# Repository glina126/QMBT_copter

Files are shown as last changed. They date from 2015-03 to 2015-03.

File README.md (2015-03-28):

# QMBT_copter
A simple, yet versatile quadcopter controller and code. Based on the Arduino platform using the Atmega328p and MPU6050.

arduino quadcopter
arduino quadcopter

QMBT with its code in the background

##Final Update:
This project is changing direction. The atmega328p microcontroller is simply insufficient for being used as a quadcopter brain. <br>
This is due to a few reasons mainly because - not enough interrupts and 8bit architecture.  <br>
The loop runs at a mere 33 miliseconds, which is not sufficient.  <br>
Also, due to the lack of interrupts, the precision at which we can sample the RC RX is very low causing noise in the system. <br>
That being said, the project is changing gears and moving on to a much better microcontroller, LPC11U35 Cortex-m0 running at 48mhz. <br> 

###This project has a few milestones that are set on its path. 
1. Create a versatile PCB which will overcome the common problems such as power distribution. 
2. Create lightweight code that will be self sufficient, aka, no external program will be needed for changing settings of the quadcopter, except for a terminal window. 
3. Ultimate goal is to have full support of peripheral devices such as a sonic distance sensor to help aid in obstacle avoidance, or a GPS unit for man-less operation. 

This is just the beginning of the project, though experimentation with the PCB have been conducted for a while now. At this point, the project is reset to a fresh start.

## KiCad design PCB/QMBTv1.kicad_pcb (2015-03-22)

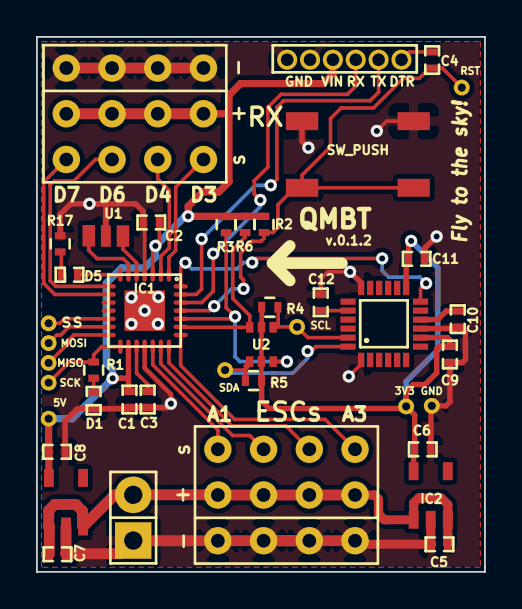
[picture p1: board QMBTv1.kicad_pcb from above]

Board: 2 copper layers, 24.9 x 29.7 mm, 42 parts (0 on the bottom side), 33 nets.

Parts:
C1, C2, C3, C4, C10, C11: 0.1uF; SMD-0402_c
C5: 1uF; SMD-0402_c
C6: 2.2uF; SMD-0402_c
C7, C8: C; SMD-0402_c
C9: 10nF; SMD-0402_c
C12: 2.2nF; SMD-0402_c
C13: 6pin_1.27mm
D1, D5: LED; SMD-0402_LED
IC1: ATMEGA328P-MM; QFN-28-4x4mm_fixed_mask
IC2, IC3: MCP1802_(Vreg); Sot-23-5
IC4: MPU6050
P9: MISO; 1x0.5mm_Through_hole2
P10: MOSI; 1x0.5mm_Through_hole2
P11: SCK; 1x0.5mm_Through_hole2
P12: RST; 1x0.5mm_Through_hole2
P14: SDA; 1x0.5mm_Through_hole2
P15: SCL; 1x0.5mm_Through_hole2
P16: SS; 1x0.5mm_Through_hole2
P17: VCC; Socket_Strip_Straight_1x02
P18: 3V3; 1x0.5mm_Through_hole2
P19: GND; 1x0.5mm_Through_hole2
P20: 5V; 1x0.5mm_Through_hole2
R1, R3, R4, R5, R6, R17: 1K; R_0402
R2: 10K; R_0402
SW1: SW_PUSH; switch_tactile_SM10
U1: ceramic_resonator; ceramic_resonator_smd
U2: BSS138DW_array
U3, U4: conn_3x4

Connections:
+3.3V: C6.1, C9.1, C11.1, IC2.5, IC4.8, IC4.13, P18.1, R4.1, R5.1, U2.2, U2.5
+5V: C1.1, C2.1, C8.1, C13.3, IC1.3, IC1.16, IC3.5, P20.1, R2.1, R3.1, R6.1, U3.5
A0: IC1.19, U4.1
A1: IC1.20, U4.2
A2: IC1.21, U4.3
A3: IC1.22, U4.4
D2: IC1.28, IC4.12
D3: IC1.1, U3.1
D4: IC1.2, U3.2
D5: D5.1, IC1.7
D6: IC1.8, U3.3
D7: IC1.9, U3.4
D10: IC1.12, P16.1
DTR: C4.1, C13.6
GND: C1.2, C2.2, C3.2, C5.2, C6.2, C7.2, C8.2, C9.2, C10.2, C11.2, C12.2, C13.1, C13.2, D1.2, IC1.4, IC1.18, IC1.d29, IC2.2, IC3.2, IC4.1, IC4.9, IC4.18, P17.1, P19.1, R17.1, SW1.2, U1.3, U3.6, U4.6
H_SCL: IC1.24, R3.2, U2.6
H_SDA: IC1.23, R6.2, U2.3
MISO: IC1.14, P9.1
MOSI: IC1.13, P10.1
unnamed: C3.1, IC1.17
unnamed: C10.1, IC4.10
unnamed: C12.1, IC4.20
unnamed: D1.1, R1.1
unnamed: D5.2, R17.2
unnamed: IC1.5, U1.1
unnamed: IC1.6, U1.2
RESET: C4.2, IC1.25, P12.1, R2.2, SW1.1
RXI: C13.4, IC1.26
SCK: IC1.15, P11.1, R1.2
SCL: IC4.23, P15.1, R4.2, U2.1
SDA: IC4.24, P14.1, R5.2, U2.4
TXD: C13.5, IC1.27
VIN: C5.1, C7.1, IC2.1, IC2.3, IC3.1, IC3.3, P17.2, U4.5

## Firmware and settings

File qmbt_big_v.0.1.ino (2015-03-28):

/****************************************************************************************
QMBT BIG V.1.0 - stable
Written by Damian Glinojecki

Features:
- Arming system 
- Flexible code to easily accommodate different structure and internals
- Spin wild (best feature!)
- Flyable, but hard to control quadcopter 
- IT WORKS! 

TO DO:
- Change platform - MBED
- Next platform is going to be a 32-bit ARM Cortex-M0 Microcontroller running at 48MHz 
- Prototyipng platform: http://developer.mbed.org/platforms/EA-LPC11U35/
- Finally getting out of the Arduino bubble. 
****************************************************************************************/

#include <Servo.h>
#include "I2Cdev.h"  // library written by jrowberg
#include "MPU6050.h" // library written by jrowberg
#include <PID_v1.h>  // library written by Beauregard

#if I2CDEV_IMPLEMENTATION == I2CDEV_ARDUINO_WIRE
    #include "Wire.h"
#endif

#define AILERON 3  // RX in pin
#define ELEVATOR 4 // RX in pin
#define RUDDER 7   // RX in pin
#define THROTTLE 6 // RX in pin

#define M1 14 // ESC motor pin 
#define M2 15 // ESC motor pin 
#define M3 16 // ESC motor pin 
#define M4 17 // ESC motor pin 

#define MIN_OUTPUT 1000 // min output in microseconds
#define MAX_OUTPUT 2000 // max output in microseconds

#define MIN_LIMIT -100 // the minimum value outputed by the PID
#define MAX_LIMIT 100  // the maximum value outputed by the PID

#define MIN_SPIN 1200 // minimal motor speed

#define INVERT_CHANNEL 3000 // constant used for inverting the channel output

MPU6050 mpu;
Servo motor[4];

// global vars
int16_t ax, ay, az; // raw values of the accelerometer output
int16_t gx, gy, gz; // raw values of the gyroscope output

uint32_t timer; // used to keep track of time
unsigned long start_time = 0; // used to measure loop cycle time in ms

double raw_x_degree = 0; // raw x angle in degrees
double raw_y_degree = 0; // raw y angle in degrees
double raw_z_degree = 0; // raw z angle in degrees

double comp_x_degree = 0; // complimentary x angle in degrees
double comp_y_degree = 0; // complimentary y angle in degrees
double comp_z_degree = 0; // complimentary z angle in degrees

double acc_x_degree = 0; // angle estimated using the accelerometer 
double acc_y_degree = 0; // angle estimated using the accelerometer

int rx_duration_last[4] = {1500,1500,1500,1000}; // used to average channels and for comparesment - safety mechanism
int rx_duration[4]; // store the ms each channel output

double input_gx, output_gx, setpoint_gx; // x axis PID
double input_gy, output_gy, setpoint_gy; // y axis PID
double input_gz, output_gz, setpoint_gz; // z axis PID

int motor_speed[4] = {MIN_OUTPUT, MIN_OUTPUT, MIN_OUTPUT, MIN_OUTPUT}; // timing of a pulse - in microseconds 
int throttle = 0; // throttle position

// PID objects
PID gx_pid(&input_gx,&output_gx,&setpoint_gx,1.8,2.0,.4,DIRECT); // 1.2, 1.0, .65
PID gy_pid(&input_gy,&output_gy,&setpoint_gy,1.8,2.0,.4,DIRECT); // 1.4, 0.9, 0.44
PID gz_pid(&input_gz,&output_gz,&setpoint_gz,1.2,0,.41,DIRECT);

// tunning variables
double pid_tune_p = 0.0;
double pid_tune_i = 0.0;
double pid_tune_d = 0.0;

bool ARMED = false; // protection against accidental motor spin
int arm_led = 5; // arm led - on when ARMED

void setup() {
  // initialize input pins
  pinMode(AILERON, INPUT);
  pinMode(ELEVATOR, INPUT);
  pinMode(RUDDER, INPUT);
  pinMode(THROTTLE, INPUT);
  
  // arm led - on when ARMED
  pinMode(arm_led, OUTPUT);
   
  // attach motor to pins
  motor[0].attach(M1);
  motor[1].attach(M2);
  motor[2].attach(M3);
  motor[3].attach(M4);
  
  // turn off all motors
  motor[0].writeMicroseconds(MIN_OUTPUT);
  motor[1].writeMicroseconds(MIN_OUTPUT);
  motor[2].writeMicroseconds(MIN_OUTPUT);
  motor[3].writeMicroseconds(MIN_OUTPUT);
  
  // join I2C bus (I2Cdev library doesn't do this automatically)
  #if I2CDEV_IMPLEMENTATION == I2CDEV_ARDUINO_WIRE
      Wire.begin();
  #elif I2CDEV_IMPLEMENTATION == I2CDEV_BUILTIN_FASTWIRE
      Fastwire::setup(400, true);
  #endif
 
  // initialize serial comm
  Serial.begin(38400);
  
  // initialize mpu6050
  mpu.initialize();
  
  // verify connection
  Serial.println("Testing device connections...");
  Serial.println(mpu.testConnection() ? "MPU6050 connection successful" : "MPU6050 connection failed");
  
  // set gyroscope and accelerometer ranges - safe to do it everytime?
  #if 1
    mpu.setFullScaleGyroRange(0x00);
    mpu.setFullScaleAccelRange(0x00); 
    mpu.setDLPFMode(0x03); //0x03
    
    Serial.print("gyro rate: ");
    Serial.println(mpu.getFullScaleGyroRange());
    Serial.print("accel rate: ");
    Serial.println(mpu.getFullScaleAccelRange());
    Serial.print("DLPFMode: ");
    Serial.println(mpu.getDLPFMode());
    delay(1500);
  #endif
  
  // initialize PID
  input_gx = output_gx = setpoint_gx = 0; // x axis PID
  input_gy =  output_gy = setpoint_gy = 0; // y axis PID
  input_gz = output_gz = setpoint_gz = 0; // z axis PID
  // set up PID for x axis
  gx_pid.SetOutputLimits(MIN_LIMIT,MAX_LIMIT); //MIN and MAX for output limits 
  gx_pid.SetSampleTime(30);
  // set up PID for y axis
  gy_pid.SetOutputLimits(MIN_LIMIT,MAX_LIMIT); 
  gy_pid.SetSampleTime(30);
  // set up PID for yaw axis
  gz_pid.SetOutputLimits(MIN_LIMIT,MAX_LIMIT);
  gz_pid.SetSampleTime(30);
  
  // initialize the timer 
  timer = micros(); 
}

void loop() {  
  // start timing loop
  start_time = millis();
    
  // get the user input
  getUserInput();
  
  arm();
  
  // populate new filtered values
  callIMU();
  
  // calculate the PID values
  callPID();
  
  // calculate new motor values 
  calculateNewMotorValues();
  
  // apply the new values to the motors
  applyToMotors();
       
  // display time per loop cycle 
  #if 0
    Serial.print("loop cycle time = ");
    Serial.println(millis() - start_time);
  #endif
  
}

void callIMU()
{
  // read raw acceletometer and gyro measurements from mpu6050
  mpu.getMotion6(&ax, &ay, &az, &gx, &gy, &gz);
  
  // check how much time has gone by
  double dt = (double)(micros() - timer) / 1000000; 
  
  // update the timer
  timer = micros(); 
  
  // display raw mpu values
  #if 0
    Serial.print("a/g:\t");
    Serial.print(ax); Serial.print("\t");
    Serial.print(ay); Serial.print("\t");
    Serial.print(az); Serial.print("\t");
    Serial.print(gx); Serial.print("\t");
    Serial.print(gy); Serial.print("\t");
    Serial.println(gz);
  #endif
  
  // calculate the angles 
  
  // convert to degrees per second
  double gyro_x_rate = gx / 131.0; 
  double gyro_y_rate = gy / 131.0; 
  double gyro_z_rate = gz / 131.0;
  
  // display degrees per second of the xyz axies
  #if 0
    Serial.print("gx/gy/gz in deg/sec = ");
    Serial.print(gyro_x_rate); Serial.print("\t");
    Serial.print(gyro_y_rate); Serial.print("\t");
    Serial.println(gyro_z_rate);
  #endif
  
  // raw gyro values in degrees
  raw_x_degree += gyro_x_rate * dt; // Calculate gyro angle without any filter
  raw_y_degree += gyro_y_rate * dt;
  raw_z_degree += gyro_z_rate * dt;
  
  // display raw degrees of the xyz axies (non-filtered)
  #if 0
    Serial.print("gx/gy/gz in deg = ");
    Serial.print(raw_x_degree); Serial.print("\t");
    Serial.print(raw_y_degree); Serial.print("\t");
    Serial.println(raw_z_degree);
  #endif
  
  // convert to angles using the accelerometer  
  acc_x_degree = atan((double) ay / sqrt((double) ax * (double) ax + (double) az * (double) az)) * RAD_TO_DEG;
  acc_y_degree = atan2((double) -ax, (double) az) * RAD_TO_DEG;
  
  // display angles estimated using the accelerameter
  #if 0
    Serial.print("ax/ay in deg = ");
    Serial.print(acc_x_degree); Serial.print("\t");
    Serial.println(acc_y_degree);
  #endif
  
  // apply complimentary filtering - kalman is too hefty for this this mcu when using pulseIn :( 
  comp_x_degree = 0.93 * (comp_x_degree + gyro_x_rate * dt) + 0.07 * acc_x_degree; // Calculate the angle using a Complimentary filter
  comp_y_degree = 0.93 * (comp_y_degree + gyro_y_rate * dt) + 0.07 * acc_y_degree;
  comp_z_degree = raw_z_degree; // no magnometer thus we cannot filter the z axis. :(
  
  // display angles estimated using the complimentary filter
  #if 1
    Serial.print("compl angles x/y/z  = ");
    Serial.print(comp_x_degree); Serial.print("\t");
    Serial.print(comp_y_degree); Serial.print("\t");
    Serial.println(comp_z_degree);
  #endif
    
}

void getUserInput()
{
  // check whats going on all the rx channels  
  // read in the 4 supported channels 
  rx_duration[0] = pulseIn(AILERON, HIGH);
  rx_duration[1] = pulseIn(ELEVATOR, HIGH);
  rx_duration[2] = pulseIn(RUDDER, HIGH);
  rx_duration[3] = INVERT_CHANNEL - pulseIn(THROTTLE, HIGH);
  
  // save teh rx duration before modifying
  int rx_temp[4];
  rx_temp[0] = rx_duration[0];
  rx_temp[1] = rx_duration[1];
  rx_temp[2] = rx_duration[2];
  rx_temp[3] = rx_duration[3];
  
  // smoothing and safety algorithm - average of the last 2 - average of the last 3 would probably better (or even a filter)
  for(int i = 0; i < 4; i++)
  {
    if(rx_duration[i] - rx_duration_last[i] > 1000)
    {
      // this is not normal. disable the quadcopter
      // not implemented for now. 
    }
    else
    {
      // average the two values together
      rx_duration[i] = (rx_duration[i] + rx_duration_last[i])/2;     
      
      // save the current value to the old one
      rx_duration_last[i] = rx_temp[i];
    }
  }
   
  // diplay miliseconds for each channel
  #if 0
    Serial.print("A/E/R/T = ");
    Serial.print(rx_duration[0]);
    Serial.print("\t");
    Serial.print(rx_duration[1]);
    Serial.print("\t");
    Serial.print(rx_duration[2]);
    Serial.print("\t");
    Serial.println(rx_duration[3]);
  #endif
}

void callPID()
{ 
  // set the new setpoint 
  long temp_n = -40.0;
  long temp_p = 40.0;
  setpoint_gx = modifiedMap(rx_duration[1], MIN_OUTPUT, MAX_OUTPUT, temp_n, temp_p);
  setpoint_gy = modifiedMap(rx_duration[0], MIN_OUTPUT, MAX_OUTPUT, -40, 40);
  setpoint_gz = modifiedMap(rx_duration[2], MIN_OUTPUT, MAX_OUTPUT, -40, 40);
      
  // display setpoint before the calculation
  #if 0
    Serial.print("PID setpoint x/y/z = "); 
    Serial.print(setpoint_gx);
    Serial.print("\t"); 
    Serial.print(setpoint_gy);
    Serial.print("\t"); 
    Serial.println(setpoint_gz);
  #endif
  
  
  // set new input
 input_gx = comp_x_degree;
 input_gy = comp_y_degree;
 input_gz = comp_z_degree;
  
  // display input_gx before the calculation
  #if 0
    Serial.print("PID input x/y/z = "); 
    Serial.print(input_gx);
    Serial.print("\t"); 
    Serial.print(input_gy);
    Serial.print("\t"); 
    Serial.println(input_gz);
  #endif
  
  // compute the PID
  gx_pid.Compute();
  gy_pid.Compute();
  gz_pid.Compute();
    
  // display raw PID values
  #if 0
    Serial.print("PID x/y/z = "); 
    Serial.print(output_gx);
    Serial.print("\t"); 
    Serial.print(output_gy);
    Serial.print("\t"); 
    Serial.println(output_gz);
  #endif
  
}

void calculateNewMotorValues()
{
  // motor_speed is to be applied to the motors.
  // we have to make sure it has been properly filtered
  // programmers fingers are really important :P
  
  // set the throttle straight from the rx
  throttle = rx_duration[3]; // number between 1000 and 2000 (theoritically) 
  
  // all motors get throttle and then are corrected by the PID
  motor_speed[0] = throttle + output_gx + output_gy ;
  motor_speed[1] = throttle + output_gx - output_gy ;
  motor_speed[2] = throttle - output_gx - output_gy ;
  motor_speed[3] = throttle - output_gx + output_gy ;
  
  // make sure that the values are in range
  for(int i = 0; i < 4; i++)
  {
    if(motor_speed[i] < MIN_SPIN)
    {
      motor_speed[i] = MIN_SPIN;
    }    
    else if(motor_speed[i] > MAX_OUTPUT)
    {
      motor_speed[i] = MAX_OUTPUT; 
    }
    
    if(ARMED && motor_speed[i] < MIN_SPIN)
    {
      motor_speed[i] = MIN_SPIN; 
    }
  }
}

int armed_counter = 0;

void arm()
{
  if(throttle < 1200 && ARMED == false && rx_duration[1] < 1300)
  {    
     Serial.print("counter = ");
     Serial.println(armed_counter);
     
     // increase armed counter
     armed_counter++;
     if(armed_counter > 40)
     {
       // reset the counter
       armed_counter = 0;
       // turn on the ARMED led
       digitalWrite(arm_led, HIGH);
       // set ARMED to true
       ARMED = true;
     }
  }
  else if(throttle < 1200 && ARMED == true && rx_duration[1] > 1700)
  {    
     Serial.print("counter = ");
     Serial.println(armed_counter);
     
     // increase armed counter
     armed_counter++;
     if(armed_counter > 40)
     {
       // reset the counter
       armed_counter = 0;
       // turn on the ARMED led
       digitalWrite(arm_led, LOW);
       // set ARMED to true
       ARMED = false;
     }
  }
  else 
  {
    armed_counter = 0;
  }  
}


void applyToMotors()
{
  if(throttle > 1200 && ARMED)
  {
    if(!gx_pid.GetMode())
    {
      Serial.println("setting to automatic");
      gx_pid.SetMode(AUTOMATIC);
      gy_pid.SetMode(AUTOMATIC);
      gz_pid.SetMode(AUTOMATIC);      
    } 
    
    motor[0].writeMicroseconds(motor_speed[0]);
    motor[1].writeMicroseconds(motor_speed[1]);
    motor[2].writeMicroseconds(motor_speed[2]);
    motor[3].writeMicroseconds(motor_speed[3]);  
  }
  else
  {
    motor[0].writeMicroseconds(MIN_OUTPUT);
    motor[1].writeMicroseconds(MIN_OUTPUT);
    motor[2].writeMicroseconds(MIN_OUTPUT);
    motor[3].writeMicroseconds(MIN_OUTPUT);
    
    gx_pid.SetMode(MANUAL);
    gy_pid.SetMode(MANUAL);
    gz_pid.SetMode(MANUAL);
    
    setpoint_gx = 0;
    setpoint_gy = 0;
    setpoint_gz = 0; 
    
    // reset the heading
    comp_z_degree = 0;
  }
  // display the new motor values
  #if 0
    Serial.print("motor values 0/1/2/3 = "); 
    Serial.print(motor_speed[0]);
    Serial.print("\t"); 
    Serial.print(motor_speed[1]);
    Serial.print("\t"); 
    Serial.print(motor_speed[2]);
    Serial.print("\t"); 
    Serial.println(motor_speed[3]);
  #endif
}

double modifiedMap(double x, double in_min, double in_max, double out_min, double out_max)
{
 double temp = (x - in_min) * (out_max - out_min) / (in_max - in_min) + out_min;
 temp = (int) (4*temp + .5);
 return (double) temp/4;
}

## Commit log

2015-02-22 initial commit. definitions and a simple relay mechanism
2015-02-22 QMBT big v.0.1 PCB
    [$AnalogReciever.sch, 2.4ghzTranciever.sch, Booster_5V.sch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]
2015-02-22 added a complementary filter and separated the IMU call into its own function
2015-02-22 added a PID algorithm
2015-03-28 more PID tunning
